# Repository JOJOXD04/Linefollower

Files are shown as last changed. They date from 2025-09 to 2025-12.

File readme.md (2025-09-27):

# LineFollower

lege repository die je als template kan gebruiken om een eigen repository te starten voor uw linefollower project

A description of my image


## specifications

microcontroller:

motors: 

h-bridge:

sensors:

batteries:

wireless communication:

distance sensor - motors:

weight:

speed:

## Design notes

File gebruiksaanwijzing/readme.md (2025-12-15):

# Gebruiksaanwijzing

### opladen / vervangen batterijen
Batterijen worden opgeladen met een lader die specifiek ontworpen is voor 18650 (Lithium) batterijen. Voor de batterijen kunnen worden ingestoken of verwijderd moet er gecontroleerd worden of de hoofdschakelaar van de linefollower uitstaat 

### draadloze communicatie
#### verbinding maken
Er wordt een hc-05 gebruikt. **Werkt alleen met android!**
Video met alle uitleg die je nodig hebt voor bluetooth module in te stellen: **https://www.youtube.com/watch?v=A0uFtI_hX6Q **

De applicatie die gebruikt werdt om de commandos te sturen is "serial bluetooth terminal", is beschikbaar op de google playstore.

#### commando's
debug  
run
stop  
set cycle [µs]  
set power [0..255]  
set diff [0..1]  
set kp [0..]  
set ki [0..]  
set kd [0..]  
calibrate black  
calibrate white  

### kalibratie
uitleg kalibratie  

### settings
De robot rijdt stabiel met volgende parameters:



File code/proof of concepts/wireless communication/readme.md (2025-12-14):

# draadloze communicatie proof of concept
minimale hard- en software waarmee aangetoond wordt dat duplex kan gecommuniceerd worden tussen de microcontroller en een smartphone, gebruik makend van [Serial Bluetooth Terminal]
<br />
### configuratie
Video met alle uitleg die je nodig hebt voor bluetooth module in te stellen:  **https://www.youtube.com/watch?v=A0uFtI_hX6Q **
### opmerkingen

### gebruiksaanwijzing
Sluit de bluetooth module en de led aan zoals op het elektrisch schema en laad de code in je arduino nano. Open de Serial Bluetooth Terminal op je smartphone. En verbind met de bluetooth module. Druk op de 3 steepjes links vanboven. Ga naar settings. Dan naar send en bij Newline duid je aan none. Dit om ervoor te zorgen dat er niet meer wordt verstuurd dan dat er word gevraagd. Ga nu terug naar het begin scherm. Nu kan er getest worden. Typ 1 voor led aan. 2 voor knipperen 3x en 0 voor de led uit te zetten.

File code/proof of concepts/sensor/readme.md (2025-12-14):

# Sensoren proof of concept

minimale hard- en software die aantoont dat minimaal 6 sensoren onafhankelijk van elkaar kunnen uitgelezen worden (geen calibratie, normalisatie of interpolatie). Hierbij moet een zo groot mogelijk bereik van de AD converter benut worden (indien van toepassing)

Sluit de sensor array aan zoals op het elektrisch schema en laad de code in je arduino nano. Open de serial monitor in arduino IDE. Hier gaan de waardes van de sensoren in komen. Controleer nu als de sensoren werken door er een wit blad en een zwart blad eens er onder te leggen.

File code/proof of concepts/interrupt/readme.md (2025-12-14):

# start/stop interrupt proof of concept
minimale hard- en software die de correcte werking van een start/stop drukknop aantoont, gebruik makend van een hardware interrupt

Sluit de drukknop en de led aan zoals op het elektrisch schema en laad de code in je arduino nano. Haal de kabel uit de arduino en zet de schakelaar dicht van de voeding. Wanneer je op de drukknop drukt zal de lamp aan gaan. Als er daarna nog eens op gedrukt wordt zal het uit gaan.

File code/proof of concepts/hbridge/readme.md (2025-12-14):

# H-Bridge proof of concept

minimale hard- & software + stappenplan dat aantoont dat 2 motoren onafhankelijk van elkaar kunnen draaien, en (traploos) regelbaar zijn in snelheid en draairichting.

Sluit de Hbrug aan zoals op het elektrisch schema en laad de code in je arduino nano. Haal de kabel uit de arduino en zet de schakelaar dicht van de voeding. De motoren beginnen te draaien.

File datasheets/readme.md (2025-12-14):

## Datasheets of the components used in this project
<br />

|Element|Link|
|---|----|
|Nano V3 Arduino:|https://www.jameco.com/Jameco/Products/ProdDS/2283855.pdf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|
|Bluetooth module (HC-05):|https://components101.com/sites/default/files/component_datasheet/HC-05%20Datasheet.pdf|
|H-brug (DRV8833):|https://components101.com/sites/default/files/component_datasheet/drv8833.pdf|

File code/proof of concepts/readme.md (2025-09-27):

# Proof of Concepts

Een proof of concept is een combinatie van minimale hard- en software om eenvoudig aan te tonen dat iets werkt.  
Proof of concepts kunnen enerzijds als eerste poging dienen om een bepaald onderdeel van het project werkend te krijgen. Anderzijds kunnen ze tijdens het debuggen van het finale project dienen als test om eventuele hardware problemen te elimineren bij onduidelijke problemen.
<br />  
<br />
Een proof of concept bestaat uit
* een elektronisch schema (indien van toepassing)
* minimale code om de voorop gestelde zaken te demonstreren
* minimale uitleg / aandachtspunten
<br />
De elektronische schakelingen van de proof of concepts komen bij voorkeur overeen met deze van de uiteindelijke linefollower, zodat de code zonder aanpassingen op het finale project kan draaien.

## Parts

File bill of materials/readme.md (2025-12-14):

## bill of materials
<br />

|volgnummer|naam|omschrijving|nieuw/recup|kostprijs/stuk|aantal|subtotaal|
|---|----|---|---|---|---|---|
|1|Tuimelschakelaar |Schakelaar voor de voeding robot|nieuw|€0,85|1|€0,85|
|2|Bluetooth module (HC-05)|Zorgt voor draadloze connectie met robot|nieuw|€9,25|1|€9,25|
|3|TT-motor (1:48)|motoren die de wielen doen draaien|nieuw|€2|2|€4|
|4|Batterijhouder(2x18650)|houder van 2 batterijen|nieuw|€1|1|€1|
|6|Oplaadbare batterij 3,6 V (2x18650)|voeding voor de onderdelen|nieuw|€6,1|2|€12,20|
|7|Nano V3 Arduino|Aansturen van onderdelen aan de hand van geschreven code|nieuw|€6,8|1|€6,8|
|8|Breadboard 400|voor componenten op te monteren|recup|/|1|/|
|9|Oplader voor batterij(2x18650)|batterijen opladen|nieuw|€12,15|1|€12,15|
|10|Jumper kabels (man-vrouw) 10cm|verbinden van componenten|nieuw|€1,7|1|€1,7|
|11|Jumper kabels (man-man) 10cm|verbinden van componenten|nieuw|€1,9|1|€1,9|
|12|H-brug (DRV8833)|Regelt snelheid en draaizin van de motoren|nieuw|€2,18|1|€2,18|
|13|Array sensor (HY-S301)|Detecteert zwarte lijn op parcour|nieuw|€2,07|1|€2,07|
|14|wiel diameter 65mm dikte 15mm|laat de robot rijden|nieuw|€0,76|2|€1,52|
|||||||€55,62|

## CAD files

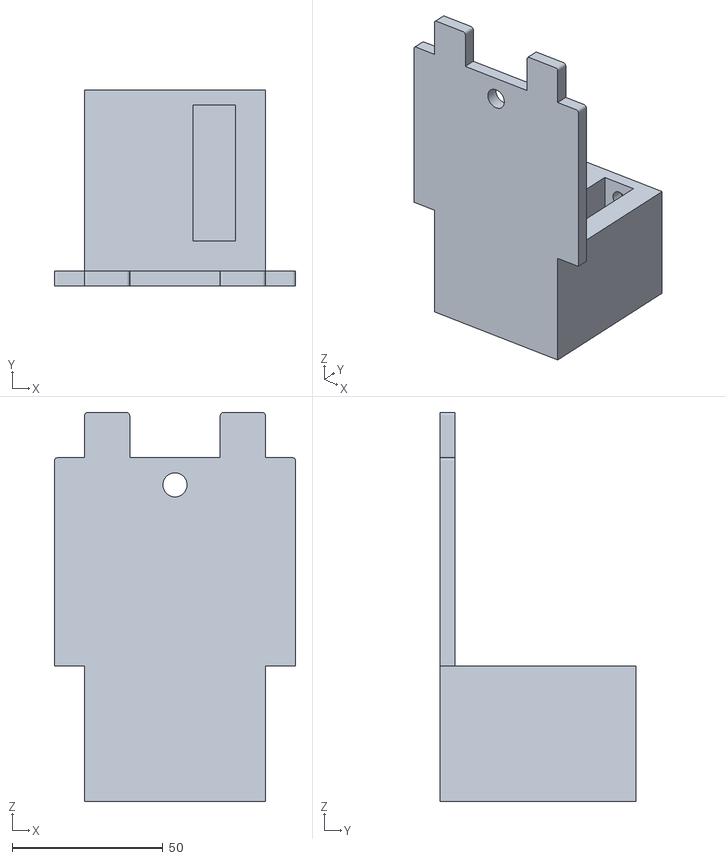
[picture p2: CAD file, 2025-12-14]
technische tekeningen/mechanisch/chassi line follower.STL
80.0 x 65.0 x 129.0

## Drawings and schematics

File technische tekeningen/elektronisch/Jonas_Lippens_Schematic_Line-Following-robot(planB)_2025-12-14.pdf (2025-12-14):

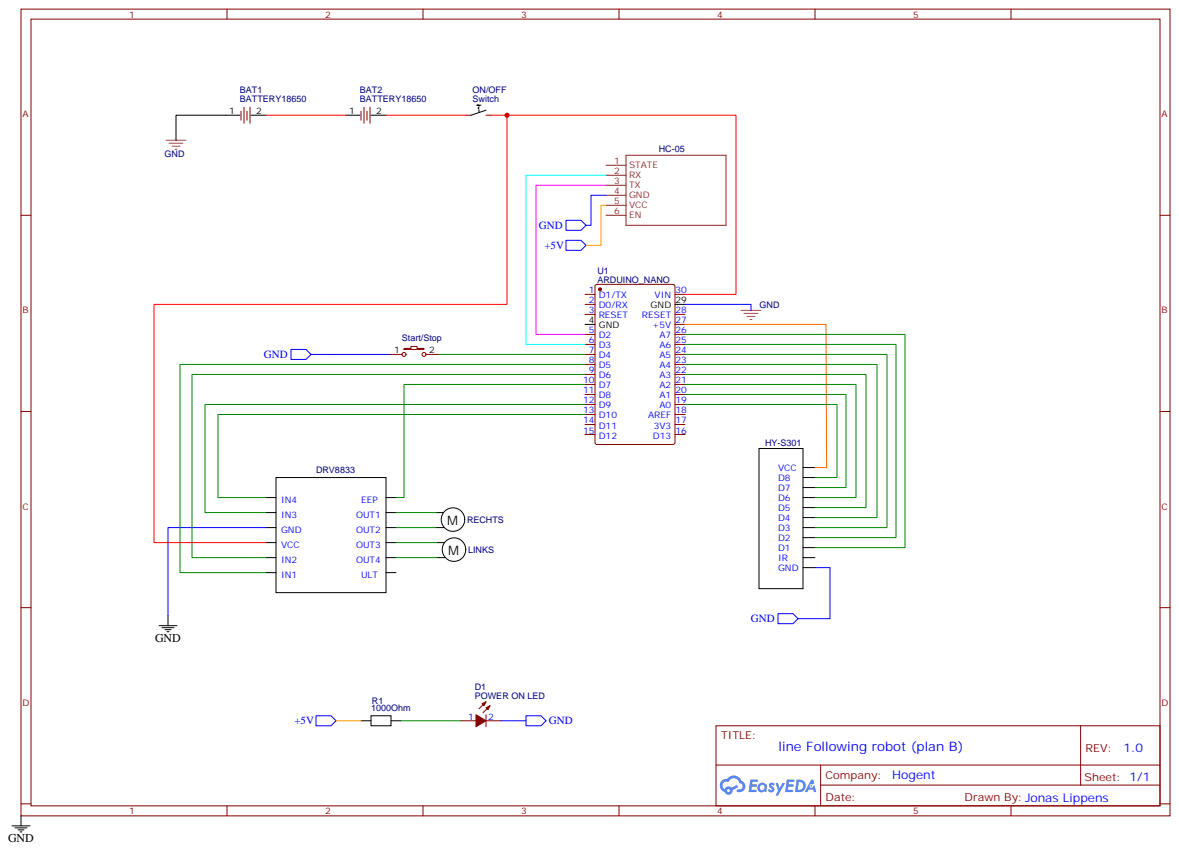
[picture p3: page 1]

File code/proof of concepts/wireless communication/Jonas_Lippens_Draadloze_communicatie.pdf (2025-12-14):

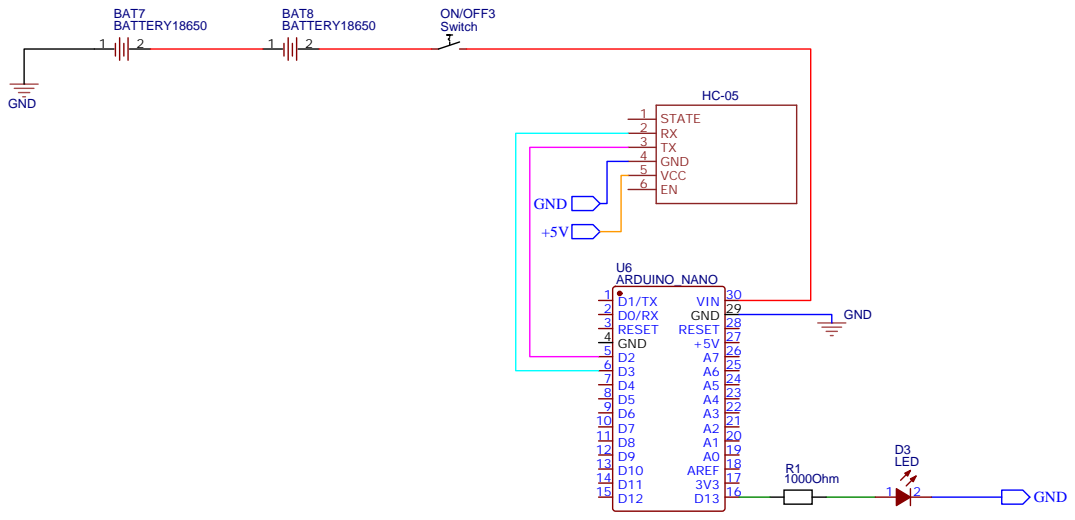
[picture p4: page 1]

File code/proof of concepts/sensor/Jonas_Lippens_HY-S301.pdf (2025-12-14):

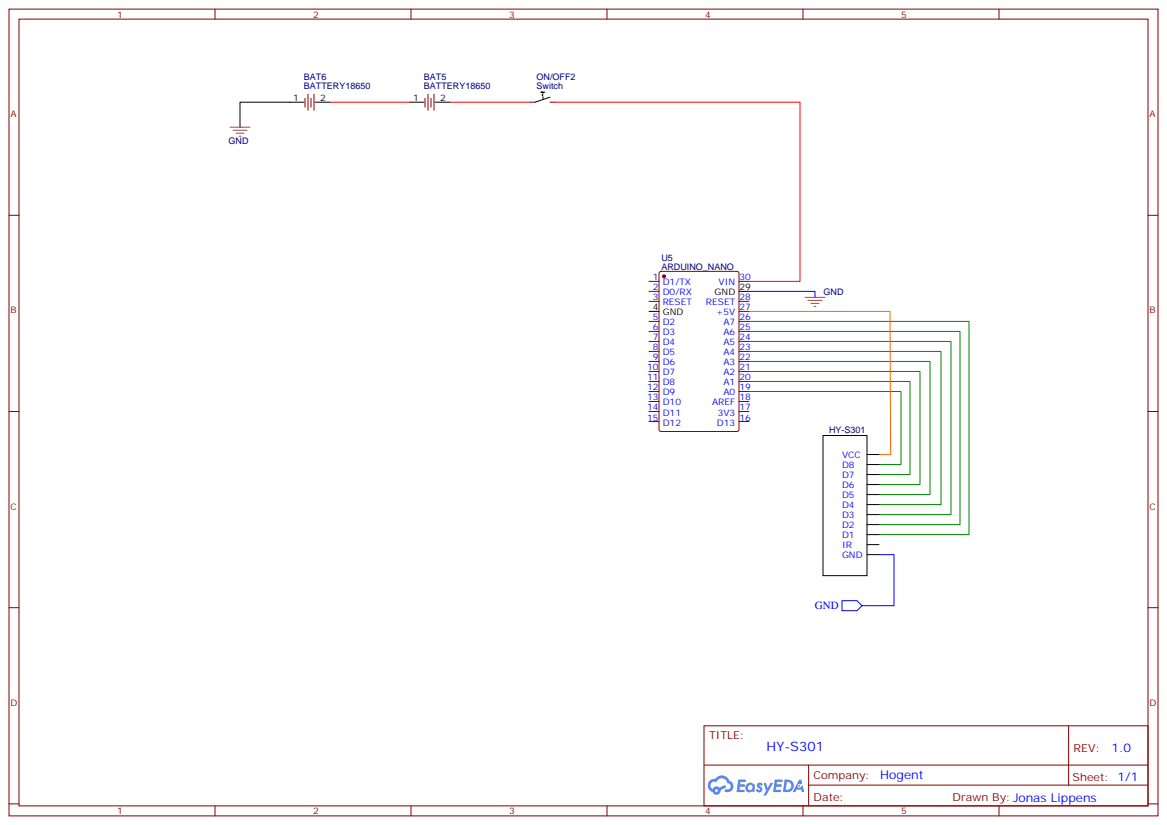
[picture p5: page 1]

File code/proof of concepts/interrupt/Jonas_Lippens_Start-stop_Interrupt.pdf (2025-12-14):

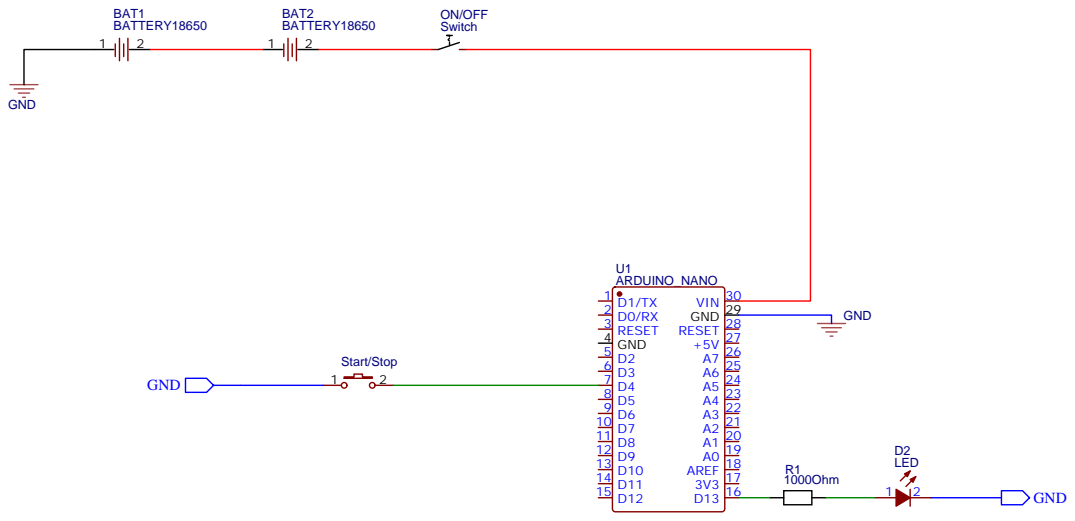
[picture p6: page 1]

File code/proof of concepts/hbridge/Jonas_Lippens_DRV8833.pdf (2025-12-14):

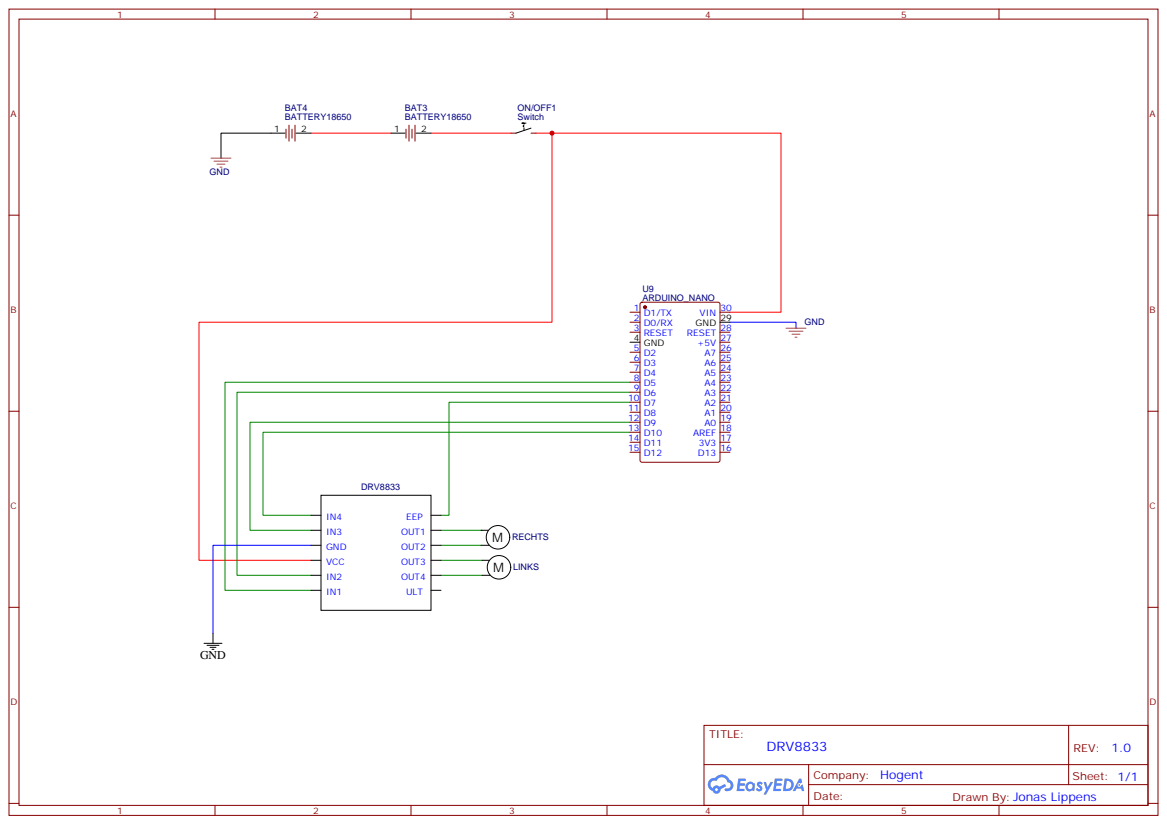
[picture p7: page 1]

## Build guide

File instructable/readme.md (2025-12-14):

# Instructable

Een instructable is een stappenplan - zonder verdere uitleg - hoe je vertrekkend van de bill of materials en gebruik makend van de technische tekeningen de robot kan nabouwen. Ook de nodige stappen om de microcontroller te compileren en te uploaden staan beschreven.  

### stap 1
Bestel alle componenten uit de bill of materials. Zoveel mogelijk van dezelfde leverancier (OTRONIC).
### stap 2
Zet de componenten op het breadbord zoals op de foto. Dit is het gemakkelijkst om te testen en om daarna op ons frame te monteren.



### stap 3
Test de componenten uit a.d.h.v de schemas en codes onder de tab code -> proof of concepts. Deze zullen een goede werking demonstreren van de componenten.

Sensoren worden best op een vaste hoogte gehouden. Om een duidelijk verschil te zien.
### stap 4
Voor het programma te uploaden naar de arduino. Moet de juiste arduino gelinkt worden aan de com poort waar de nano v3 arduino mee verbonden is in arduino IDE. Hiervoor moet eerst de bibliotheek **Arduino AVR boards** geinstalleerd worden. Ga hiervoor naar Tools helemaal vanboven op het scherm -> boards -> boards manager. Als het geinstalleerd is kan de juiste com poort veranderd worden naar de naam van de microcontroller. Om de juiste COM poort te vinden ga naar apparaatbeheer (op de laptop/pc) -> poort -> Hier vindt u de naam USB-SERIAL CH340 dit is de microcontroller. Ga nu naar arduino IDE en verbind de juiste COM poort met de naam **Arduino nano**. Als dit gedaan is kan de code geupload worden naar de Nano V3 arduino.
### stap 5
Print het frame dat te vinden is onder technische tekeningen -> mechanisch. Hier kan het stl bestand gevonden worden. 
### stap 6
Zaag een stuk van een slotbout zet er 2 rondellen van 1mm dikte op (wordt gebruikt als volgwiel). Steek het in het gat dat in het frame zit met de bolle kant naar beneden. Lijm het vast aan het frame met een lijmpistool.



### stap 7
Maak nu een gleuf 5mm van de batterij houder box voor de sensor. Groot genoeg zodat de draden erin kunnen van de sensor. De sensor zat eerst helemaal vanvoor maar dit geeft problemen voor te korte bochten. Daarom word de sensor zo dicht mogelijk geplaatst bij de wielen.
### stap 8
Neem een lijmpistool en lijm de motoren en de sensor array aan het frame.
### stap 9
Verbind nu alles met elkaar, Zoals op het schema. Dit staat onder technische tekeningen -> elektronisch.

Het zou er nu zo ongeveer moeten uitzien:



### stap 10 
Upload de final code. De follower heeft nu de mogelijkheid om de lijn te volgen.
### stap 11
Print de parcours. Steek de batterijen in de houder en zet de schakelaar aan. De arduino, apparte led, H-brug en blutooth module zouden nu moeten oplichten.
### stap 12 
Verbind met de smartphone met de Follower en test. Pas de waarde aan van de PID regelaar zodat de lijn goed gevolgd wordt.

Vergeet niet opnieuw wit en zwart te calibreren op het parcour!
Veel plezier!

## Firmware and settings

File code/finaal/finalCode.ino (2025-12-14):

#include "SerialCommand.h"
#include "EEPROMAnything.h"
#include <SoftwareSerial.h>

// HC-05 op D2 (RX van Arduino) en D3 (TX van Arduino)
SoftwareSerial BT(2, 3); // RX, TX

#define SerialPort BT
#define Baudrate 9600

// Motor pinnen
#define MotorLeftForward 5
#define MotorLeftBackward 6
#define MotorRightForward 9
#define MotorRightBackward 10

// IR LED en enable pin
const int IR = 12;
const int EEP = 7;

// SerialCommand object
SerialCommand sCmd(SerialPort);

// PID parameters en variabelen
struct param_t {
  unsigned long cycleTime;
  int black[8];
  int white[8];
  float diff;
  float kp;
  int power;
  float ki;
  float kd;
} params;

const int sensor[] = {A0, A1, A2, A3, A4, A5, A6, A7};// omgedraaid 
int normalised[8];
float debugposition;
float output;
float error;
float iTerm = 0;
float lastErr;

bool run = false;
unsigned long previous, calculationTime;

// Power ramp variabele
int powerCmd = 0;

void setup() {
  pinMode(MotorLeftForward, OUTPUT);
  pinMode(MotorLeftBackward, OUTPUT);
  pinMode(MotorRightForward, OUTPUT);
  pinMode(MotorRightBackward, OUTPUT);

  pinMode(EEP, OUTPUT);
  digitalWrite(EEP, HIGH); // enable H-brug

  pinMode(IR, OUTPUT);
  digitalWrite(IR, HIGH); // IR LED aan

  SerialPort.begin(Baudrate);

  // Commando's registreren
  sCmd.addCommand("set", onSet);
  sCmd.addCommand("debug", onDebug);
  sCmd.addCommand("calibrate", onCalibrate);
  sCmd.addCommand("run", onRun);
  sCmd.addCommand("stop", onStop);
  sCmd.addCommand("toggle", onToggle);
  sCmd.setDefaultHandler(onUnknownCommand);

  EEPROM_readAnything(0, params);
  SerialPort.println("ready");
}

void loop() {
  sCmd.readSerial();

  unsigned long current = micros();
  if (current - previous >= params.cycleTime) {
    previous = current;

    // Normaliseer sensoren
    for (int i = 0; i < 8; i++) {
      normalised[i] = map(analogRead(sensor[i]), params.black[i], params.white[i], 0, 1000);
    }

    // Positie bepalen
    int index = 0;
    for (int i = 1; i < 8; i++) if (normalised[i] < normalised[index]) index = i;

    if (normalised[index] > 950) run = false; // lijnverlies-drempel

    float position;
    if (index == 0) position = -30;
    else if (index == 7) position = 30;
    else {
      int sNul = normalised[index];
      int sMinEen = normalised[index-1];
      int sPlusEen = normalised[index+1];

      float b = (sPlusEen - sMinEen) / 2.0;
      float a = sPlusEen - b - sNul;

      position = -b / (2 * a);
      position += index;
      position -= 3.5;
      position *= 9.525; // afstand sensoren
    }
    debugposition = position;

    // PID-regelaar
    error = -position;
    output = error * params.kp;

    iTerm += params.ki * error;
    iTerm = constrain(iTerm, -510, 510);
    output += iTerm;

    output += params.kd * (error - lastErr);
    lastErr = error;

    output = constrain(output, -510, 510);

    // Power ramp
    int target = run ? params.power : 0;
    int step = 3; // max verandering per cyclus
    if (powerCmd < target) powerCmd = min(powerCmd + step, target);
    else if (powerCmd > target) powerCmd = max(powerCmd - step, target);

    // Turn-cap
    int turn = (int)(params.diff * output);
    turn = constrain(turn, -120, 120);

    // Nieuwe motor-mix
    int powerLeft  = run ? constrain(powerCmd + turn, -255, 255) : 0;
    int powerRight = run ? constrain(powerCmd - turn, -255, 255) : 0;

    // Motoren aansturen
    analogWrite(MotorLeftForward,  powerLeft  > 0 ? powerLeft  : 0);
    analogWrite(MotorLeftBackward, powerLeft  < 0 ? -powerLeft : 0);
    analogWrite(MotorRightForward, powerRight > 0 ? powerRight : 0);
    analogWrite(MotorRightBackward,powerRight < 0 ? -powerRight: 0);
  }

  unsigned long difference = micros() - current;
  if (difference > calculationTime) calculationTime = difference;
}

// Onbekend commando
void onUnknownCommand(char *command) {
  SerialPort.print("unknown command: \"");
  SerialPort.print(command);
  SerialPort.println("\"");
}

// SET-commando
void onSet() {
  char* param = sCmd.next();
  char* value = sCmd.next();  

  if (!param || !value) {
    SerialPort.println("set: missing param or value");
    return;
  }

  if (strcmp(param, "cycle") == 0) {
    long newCycleTime = atol(value);
    if (newCycleTime <= 0) { SerialPort.println("cycle must be > 0"); return; }
    float ratio = ((float)newCycleTime) / ((float)params.cycleTime == 0 ? 1.0f : (float)params.cycleTime);
    params.ki *= ratio;
    params.kd /= ratio;
    params.cycleTime = newCycleTime;
  }
  else if (strcmp(param, "ki") == 0) {
    float cycleTimeInSec = ((float)params.cycleTime) / 1000000.0f;
    params.ki = atof(value) * (cycleTimeInSec > 0 ? cycleTimeInSec : 1.0f);
  }
  else if (strcmp(param, "kd") == 0) {
    float cycleTimeInSec = ((float)params.cycleTime) / 1000000.0f;
    params.kd = atof(value) / (cycleTimeInSec > 0 ? cycleTimeInSec : 1.0f);
  }
  else if (strcmp(param, "power") == 0) params.power = atol(value);
  else if (strcmp(param, "diff") == 0) params.diff = atof(value);
  else if (strcmp(param, "kp") == 0) params.kp = atof(value);
  else {
    SerialPort.println("unknown set param");
    return;
  }

  EEPROM_writeAnything(0, params);
  SerialPort.println("ready 1");
}

// DEBUG-commando
void onDebug() {
  SerialPort.print("cycle time: ");
  SerialPort.println(params.cycleTime);

  SerialPort.print("black: ");
  for (int i = 0; i < 8; i++) { SerialPort.print(params.black[i]); SerialPort.print(" "); }
  SerialPort.println();

  SerialPort.print("white: ");
  for (int i = 0; i < 8; i++) { SerialPort.print(params.white[i]); SerialPort.print(" "); }
  SerialPort.println();

  SerialPort.print("Normalised: ");
  for (int i = 0; i < 8; i++) { SerialPort.print(normalised[i]); SerialPort.print(" "); }
  SerialPort.println();

  SerialPort.print("position: "); SerialPort.println(debugposition);
  SerialPort.print("Power: "); SerialPort.println(params.power);
  SerialPort.print("diff: "); SerialPort.println(params.diff);
  SerialPort.print("kp: "); SerialPort.println(params.kp);

  float cycleTimeInSec = ((float)params.cycleTime) / 1000000.0f;
  float ki = cycleTimeInSec > 0 ? (params.ki / cycleTimeInSec) : 0;
  SerialPort.print("Ki: "); SerialPort.println(ki);

  float kd = cycleTimeInSec > 0 ? (params.kd * cycleTimeInSec) : 0;
  SerialPort.print("Kd: "); SerialPort.println(kd);

  SerialPort.print("RUN: "); SerialPort.println(run ? "ON" : "OFF");

  SerialPort.print("calculation time: ");
  SerialPort.println(calculationTime);
  calculationTime = 0;
}

// CALIBRATE-commando
void onCalibrate() {
  char* param = sCmd.next();
  if (!param) {
    SerialPort.println("calibrate: missing 'black' or 'white'");
    return;
  }

  if (strcmp(param, "black") == 0) {
    SerialPort.print("calibrating black...");
    for (int i = 0; i < 8; i++) params.black[i] = analogRead(sensor[i]);
    SerialPort.println("done");
  }
  else if (strcmp(param, "white") == 0) {
    SerialPort.print("calibrating white...");
    for (int i = 0; i < 8; i++) params.white[i] = analogRead(sensor[i]);
    SerialPort.println("done");
  }
  else {
    SerialPort.println("calibrate: unknown arg (use 'black' or 'white')");
    return;
  }

  EEPROM_writeAnything(0, params);
  SerialPort.println("ready 2");
}

// RUN-commando
void onRun() {
  run = true;
  iTerm = 0; // integrator reset bij start
  SerialPort.println("RUN ON");
}

// STOP-commando
void onStop() {
  run = false;
  SerialPort.println("RUN OFF");
}

// TOGGLE-commando
void onToggle() {
  run = !run;
  iTerm = 0;
  SerialPort.print("Run state: ");
  SerialPort.println(run ? "ON" : "OFF");
}

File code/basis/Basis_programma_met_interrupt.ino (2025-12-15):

#include "SerialCommand.h"
#include "EEPROMAnything.h"

#define SerialPort Serial
#define Baudrate 115200

SerialCommand sCmd(SerialPort);
bool debug;
unsigned long previous, calculationTime;

struct param_t
{
  unsigned long cycleTime;
  /* andere parameters die in het eeprom geheugen moeten opgeslagen worden voeg je hier toe ... */
} params;

//TOEGEVOEGD: run-state en knop
const uint8_t BUTTON_PIN = 4;       // hardware drukknop
volatile bool running = false;      // run/stop status

// eenvoudige debounce
unsigned long lastDebounceTime = 0;
const unsigned long debounceDelay = 50; // ms
int lastButtonReading = HIGH;       // omdat INPUT_PULLUP: HIGH = niet ingedrukt
int stableButtonState = HIGH;       // huidige stabiele toestand


void setup()
{
  SerialPort.begin(Baudrate);

  sCmd.addCommand("set", onSet);
  sCmd.addCommand("debug", onDebug);
  sCmd.setDefaultHandler(onUnknownCommand);


  //TOEGEVOEGD: extra start/stop commands 
  sCmd.addCommand("start", onStart);  // via Bluetooth/Serial starten
  sCmd.addCommand("stop", onStop);    // via Bluetooth/Serial stoppen
  

  EEPROM_readAnything(0, params);

//TOEGEVOEGD: knop init
  pinMode(BUTTON_PIN, INPUT_PULLUP);  // interne pull-up, knop naar GND
 

  pinMode(13, OUTPUT);
  SerialPort.println("ready");
}

void loop()
{
  sCmd.readSerial();

  //TOEGEVOEGD: hardware knop debounce en toggle
  int reading = digitalRead(BUTTON_PIN);
  if (reading != lastButtonReading) {
    lastDebounceTime = millis();      // ingang veranderde: start debounce timer
  }
  lastButtonReading = reading;

  if ((millis() - lastDebounceTime) > debounceDelay) {
    // stabiele toestand bereikt
    if (reading != stableButtonState) {
      stableButtonState = reading;
      // detecteer een knopdruk (falling edge: van HIGH naar LOW)
      if (stableButtonState == LOW) {
        running = !running;           // toggle run/stop
        digitalWrite(13, running ? HIGH : LOW);
        SerialPort.print("state: ");
        SerialPort.println(running ? "running" : "stopped");
      }
    }
  }
  /* ========================================================================================= */

  unsigned long current = micros();
  if (current - previous >= params.cycleTime)
  {
    previous = current;

    if (running) {
      /* code die cyclisch moet uitgevoerd worden programmeer je hier ... */
    }
  }

  unsigned long difference = micros() - current;
  if (difference > calculationTime) calculationTime = difference;
}

void onUnknownCommand(char *command)
{
  SerialPort.print("unknown command: \"");
  SerialPort.print(command);
  SerialPort.println("\"");
}

void onSet()
{
  char* param = sCmd.next();
  char* value = sCmd.next();  
  
  if (strcmp(param, "cycle") == 0) params.cycleTime = atol(value);
  /* parameters een nieuwe waarde geven via het set commando doe je hier ... */
  
  EEPROM_writeAnything(0, params);
}

void onDebug()
{
  SerialPort.print("cycle time: ");
  SerialPort.println(params.cycleTime);
  
  /* parameters weergeven met behulp van het debug commando doe je hier ... */
  
  SerialPort.print("calculation time: ");
  SerialPort.println(calculationTime);
  calculationTime = 0;
}

/* ===================== TOEGEVOEGD: start/stop handlers ===================== */
void onStart() {
  running = true;
  digitalWrite(13, HIGH);
  SerialPort.println("started");
}

void onStop() {
  running = false;
  digitalWrite(13, LOW);
  SerialPort.println("stopped");
}
